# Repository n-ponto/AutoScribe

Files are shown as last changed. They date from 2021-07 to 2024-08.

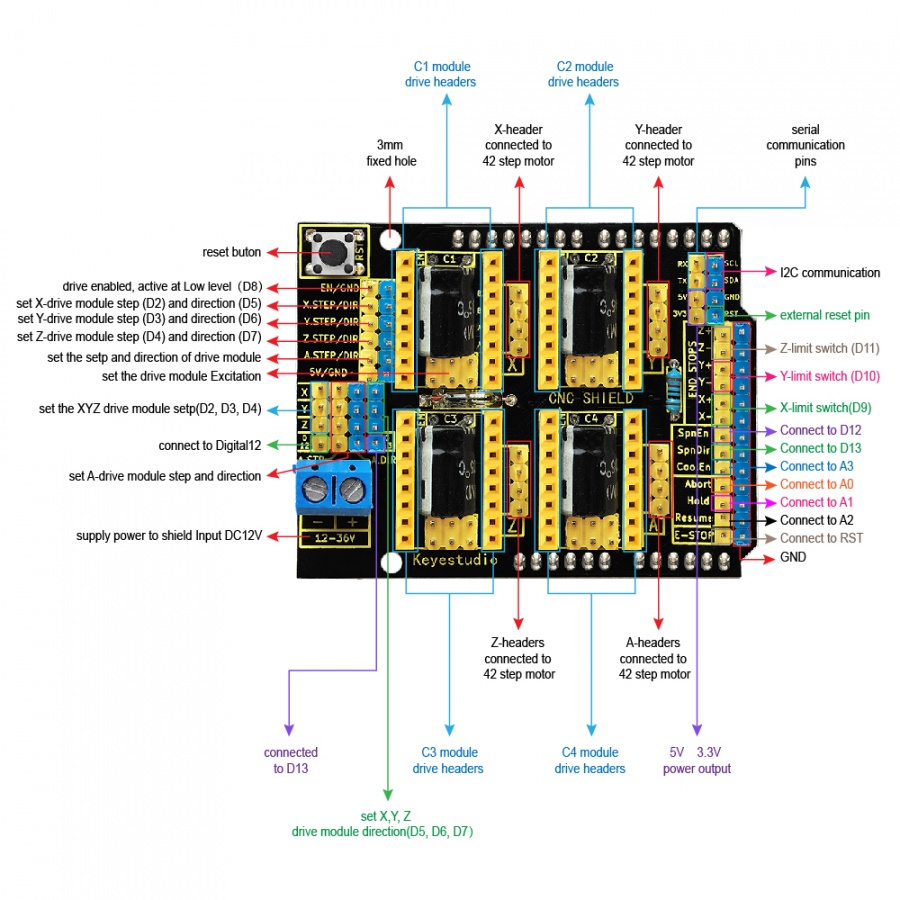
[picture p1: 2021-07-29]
images/cncsheild_wiring.jpg

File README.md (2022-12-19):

# AutoScribe

AutoScribe is a drawing machine capable of making any piece of art that can be drawn with pen on paper. On a PC, it converts scalable vector graphic (SVG) images into a set of points which are sent to the Arduino and drawn. 

## Video

Watch the video (https://youtu.be/xKn2pY1tWtM)

https://www.youtube.com/watch?v=xKn2pY1tWtM

# Background

## Inspiration

I was actually first inspired to work on this project because I enjoyed the feeling of handwritten notes, but was tired of hand cramps and sore wrists. If only there was a way to be able to combine the convenience of typing or dictating with the great feeling of pen on paper! Having seen 3D printers, laser cutters, and other CNC machines, I had the idea for a CNC drawing machine. After a quick search I found they already existed (no big suprise), but they were a bit pricy. I had some experience working with software, an Arduino, circuits, and 3D printing, how difficult would it really be to build one of these drawing machines myself? Turns out, it's actually pretty difficult -- especially when you're deadset on writing all the software yourself from scratch -- but that's why I think it's worth documenting my experience building this thing! 

## Refrences 

Along the way I found some sources which really helped get me off the ground and inspire some of my design choices:

**AxiDraw**

[AxiDraw](https://axidraw.com/) is a company which sells a range of similar writing and drawing machines. They seem to work extremely well and were a great proof of concept for me to justify the time I put into this project.

**Instructables 4xiDraw**

For most of the physical design of the machine I refrenced this instructables page titled [4xiDraw]((https://www.instructables.com/4xiDraw/)). At a glance the design is nearly the same, and I actually used the 3D models from that page in my first iteration of the hardware.

**Crazy Engineer’s Drawing Robot**

[CNC Drawbot](https://www.arnabkumardas.com/cnc.html) is another great refrence for a similar project. The page has a great bill of materials, and does things a bit different from 4xiDraw.

**Improvements in this Project** 

In my opinion, the physical design of the 3D printed parts for this project are quite a bit sleeker than others. I wanted to try to create a design took up minimal desk space and showed off the other pieces of hardware.

# Software

There are two main pieces of software for this project: (1) the C/C++ code that runs on the Arduino, and (2) the Python code that runs on a computer to convert SVGs into Ncode, send the Ncode to the Arduino, and actsas a GUI for easily using all the features of the drawing machine. 

## Arduino Code

This is all in the in the `Arduino_v2` directory, and check out the README in that directory to read more about the details of how the code works.

## Python Code

This code is mostly in the `Frames` and `Tools` directories. `Tools` contains most of the behind-the-scenes logic for converting SVGs into Ncode, sending Ncode to the Arduino, and some extra files for debugging and validating the results. `Frames` contains the code for the GUI. The `OverSerialTests` directory also has some lightweight code for testing the connection between the serial connection between the computer and the Ardiuno without needing to start the entire GUI.

# Graphical User Interface (GUI)

The GUI was written using the [tkinter](https://docs.python.org/3/library/tkinter.html) package. To start the GUI run 

```python ./GUI.py```

The GUI has 3 different tabs: Settings, Manual Control, and Drawing.

## Settings Tab

<img src="./readme_images/settings_tab.jpg" alt="Settings Tab Screenshot" width="300"/>

The settings tab is really just for adjusting the height of the pen, the "Up height" is the angle
of the pen's servo motor when the pen is off the paper, and "Down height" is when the pen is on the paper. As the angle increases the pen gets closer to the table. 

The user can use the arrow keys to fine tune these angles, and the pen on the machine will move in real time to make this process easier. When both the angles are correct pressing "Save angles" will preserve the current angles when drawing.

## Manual Control Tab

<img src="./readme_images/manual_control_tab.jpg" alt="Manual Control Tab Screenshot" width="300"/>

The manual control tab is mostly for debugging and playing around. It also uses the same pen height settings from the Settings Tab, so it's useful for checking that the pen height is correct for good ink flow while drawing. 

When not manually controlling or drawing, the stepper motors of the machine are unlocked and can be moved by hand. Once "Start manual control" is clicked, the motors will lock, and then the arrow keys can be used to control the motors. Pressing a single key will only move a single motor, (for example: pressing up and right will move both motors, up and down will do nothing). Because of the layout of the machine, when only one motor is moving, the pen will move diagonally with respect to the base. 

Holding the space bar will move the pen down to the paper.

## Drawing Tab

<img src="./readme_images/drawing_tab.jpg" alt="Manual Control Tab Screenshot" width="300"/>

The drawing tab is for selecting a `.ncode` file, vizualizing it, then sending to the Arduino. Clicking "Select File" will open a standard file selection dialog. Once a file is chosen, the path will appear where the "Please select a file" text is, and the "Vizualize" and "Send Ncode" buttons will unlock. 

Clicking the "Vizualize" button will create a new window to see what the Ncode should look like once drawn, like this: 

<img src="./readme_images/parrot_viz.jpg" alt="Manual Control Tab Screenshot" width="200"/>

Usually the vizualized images will appear more pixelated than you'd expect to see from the drawing machine. The light gray lines show the path the pen will take raised off the paper, and the blue lines show the path on the paper.

Clicking "Send Ncode" will immediately begin streaming commands to the drawing machine, and while drawing pressing "Cancel" will cause the machine to immediately stop.

# Hardware

The models for all the 3D printed pieces are in the `Models` directory. 

## Bill of Materials

| Count       | Name        | Notes        |
| --- | --- | --- |
| 1 | Arduino UNO | |
| 1 | USB cable | this should come with the Arduino
| 1 | CNC shield | connects the Arduino to the stepper motors
| 2 | Pololu stepsticks | these go on top of the CNC shield to interface with the stepper motors
| 2 | nema 17 stepper motors | 3D printer motors for moving the arm |
| 1 | micro servo SG90 | servo for moving the pen up and down |
| 1 | 12V 2A power supply | The USB connection from the computer won't be enough power for the stepper motors. Also, make sure this comes with the right connector to plug into the CNC shield somehow |
| 4 | 8mm smooth steel rods | whatever length you want for the drawing machine, I used 330mm |
| 8 | LM8UU | linear bearings for sliding along the smooth steel rods
| 2 | 20-tooth GT2 pulleys | go on top of the stepper motors for moving the belts
| 1 | GT2 belt | length depends on dimensions of your machine, can always cut one that's too long
| 10 | F623ZZ bearings | ball bearings for where the belt freely spins through the hub and by the pen |
| 2 | M10 threaded rods | these go through the two ends of the base to hold it together (have to be as long as the smooth steel rods)
| 8 | M10 nuts | two for each end of each rod |
| 8 | M10 washers | one for each M10 nut |
| X | Pack of M3 30mm, 16mm, 6mm screws, nuts, and washers | Need at least 8 of each screw, 12 nuts, and 4 washers
| 2 | 4mm OD x 100mm length rod | I used steel, 4xiDraw recommends carbon fiber. Pen slides along these. |
# Getting Started

All the info for downloading the software and getting started yourself.

## Installation

Specifications: Developed on Windows 10 using Python version 3.9.1

First clone the repo:

`git clone https://github.com/n-ponto/AutoScribe.git`

Then install the Python modules:

`pip install -r requirements.txt`

<details>
<summary>I recommend not trying to use Anaconda. Why not Anaconda?</summary>
<br>
Anaconda is a great tool to aid in Python package management.

<br>
I recommend not using Anaconda because there are some issues with installing the bezier module within the Anaconda environment. This is only required for the ParseSvg.py script, so if you don't plan to create any of your own images and just rely on the ncode files already provided in this repo, then there's no need to install the bezier module.
</details> <br> 

## Uploading to the Arduino
In order to upload the C++ code to the Aruino, the easiest way is to use the [Arduino IDE](https://www.arduino.cc/en/software). From the Aruino IDE, you'll want to open the main file at `Arduino_v2/Arduino_v2.ino`. This should open the entire Arduino project (all the files in the `Arduino_v2` folder). Then upload the code by clicking the right arrow in the top left corner of the IDE.

# Creating New Images

### Creating SVG files

Creating an SVG file is the first step in drawing something. All that really matters in this file is the Path objects, because these are what get turned into Ncode. I like using the free software [Inkscape](https://inkscape.org/) for making and working with SVGs. Inkscape has a built-in "Trace Bitmap" function to get a SVG path from a standard raster image. Usually I find that I need to manually touch up the SVG paths a bit after using this tool.

### Converting SVG files to NCODE

Once you have an SVG of a file you'd like to draw, it needs to be converted to Ncode. To do this, run:

```
python ParseSvg.py path/to/file.svg
```

`ParseSvg.py` can also directly vizualize the ncode or can take a custom save path for the Ncode file. For more info, use:
```
py ParseSvg.py -h
```

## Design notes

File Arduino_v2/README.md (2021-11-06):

# Arduino

## Overview
This is the code to run on the Arduino. It's responsible for accepting commands
from the computer over serial communication and controlling the two stepper and
one servo motors which make up the drawing machine. By accepting commands from
the computer it's able to draw images using a pen.

---

# Technical Details

## Runtime Modes
These influence how the Arduino reads information from the serial and
acts on that information.

**1. [Accepting Commands](#accepting-commands-mode)** - listens for commands over serial.

**2. [Manual Control](#manual-control-mode)** - used to manually control the movement of drawing machine in real time

**3. [Drawing](#drawing-mode)** - used to draw an image by interpreting instructions over serial

## Accepting Commands mode
Listens to serial connection for one byte commands from the list of commands below. Generally, if the command can be completed quickly or requires reading a predetermined amount of data from serial, it is executed in the Accepting Commands runtime mode before listening for the next command. If the command is to switch commands, then the Arduino will switch remain in the other runtime mode until receiving a signal to return to this mode.

| Command | Description |
| --- | --- |
| SET_PEN_RANGE | Used to define the top and bottom boundaries of the pen's movement. Will listen for two more bytes, one byte each for the minimum and maximum angle for the pens movement.  |
| CHANGE_PEN_ANGLE | Used to immediately change the current angle of the pen. This can be useful when trying to determine the optimal pen range. It will listen for one more byte for the angle to move the pen (i.e. the servo motor). | 
| MOVE_TO_COORDINATE | Used to immediately change the current location of the pen. It will listent for 4 total more bytes, two 2B integers for the x and y coordinates. | 
| RESET_HOME | Used to reset the home value of the steppers. When this command is executed the current location of the end effector will be considered the origin. |
| ENTER_DRAW_MODE | Will go into Drawing mode.  |
| ENTER_MANUAL_CONTROL_MODE | Will go into Manual Control mode. |
| SET_STEPPER_DELAY | Sets the delay between signals to the steppers. This value is directly related to the movement speed of the steppers. Should be calibrated to optimize between speed and minimal shaking. |

## Manual Control mode
After entering this mode, it will continuously listen for single byte packets indicating how to move. These instructions will either move the pen up/down, or will indicate how to move the steppers. If this mode receives the instruction to stop, it will return to the accepting commands mode.

## Drawing mode 
After entering this mode, it will continuously listen for 4 byte packets, where each packet will contain a set of two 2-byte coordinates.

The maximum coordinate range of the drawing machine can be represented using only 11-bits, meaning that each 16-bit coordinate dimension has 5 bits left over. These extra bits are used to encode additional information: pen up, pen down, and to end drawing mode.

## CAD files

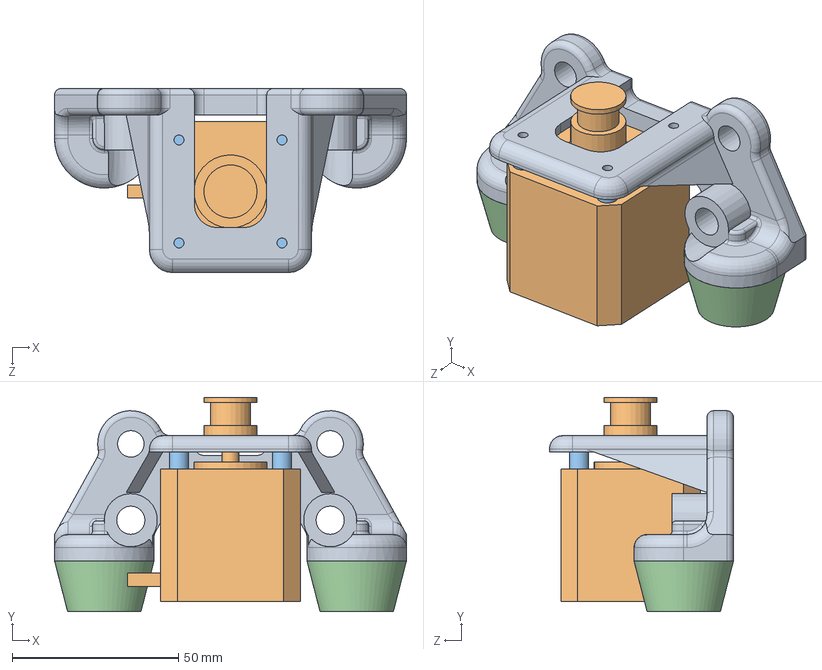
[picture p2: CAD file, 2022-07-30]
models/assembly_legs.SLDASM
105.9 x 64.5 x 55.4 mm
legs
stepper
anti-vibration screw x 4
rubber foot^assembly_legs x 2

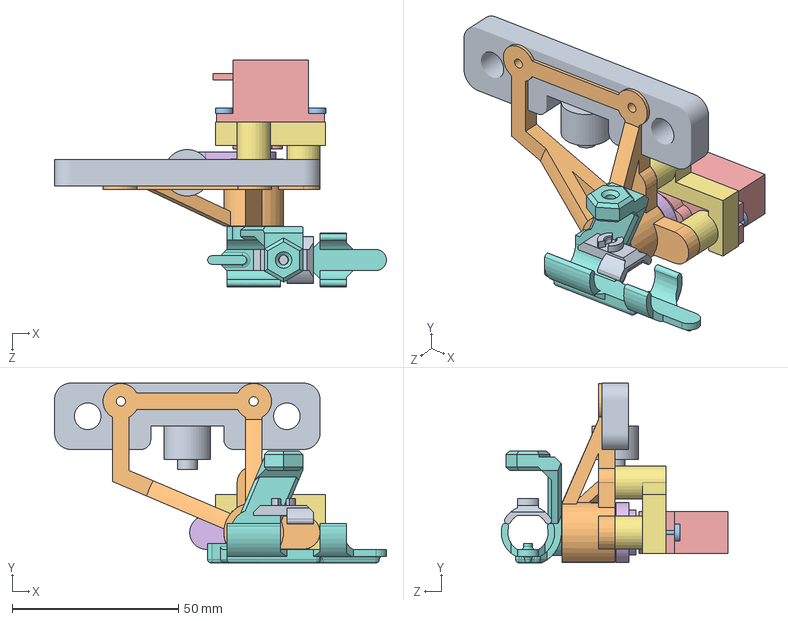
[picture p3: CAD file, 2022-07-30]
models/end_effector/v2/end_effector_assembly_v2.SLDASM
100.0 x 54.2 x 68.2 mm
mount^end_effector_assembly_v2
servo_screw x 2
servo_arm
servo
driver^end_effector_assembly_v2
servo_mount^end_effector_assembly_v2
pen holder^end_effector_assembly_v2
pen_press^end_effector_assembly_v2

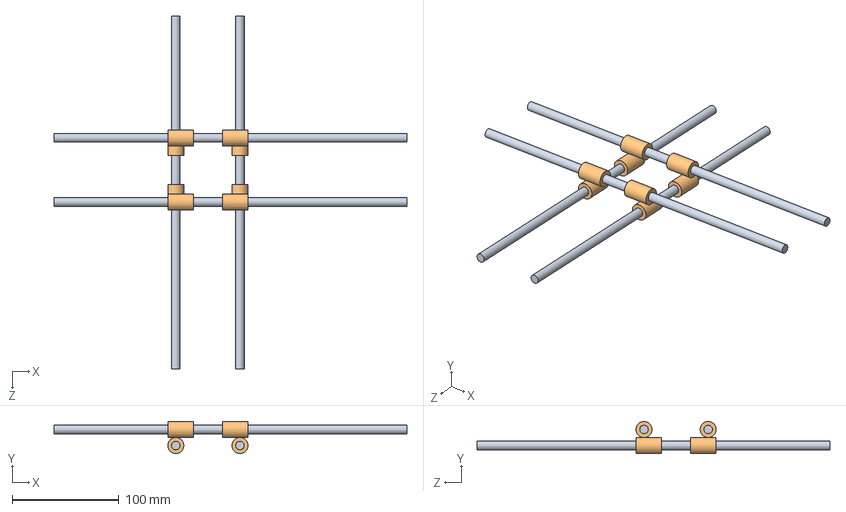
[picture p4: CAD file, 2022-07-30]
models/hub/slider_refrence/slider.SLDASM
330.0 x 30.0 x 330.0 mm
rod x 4
linear_bearing x 8

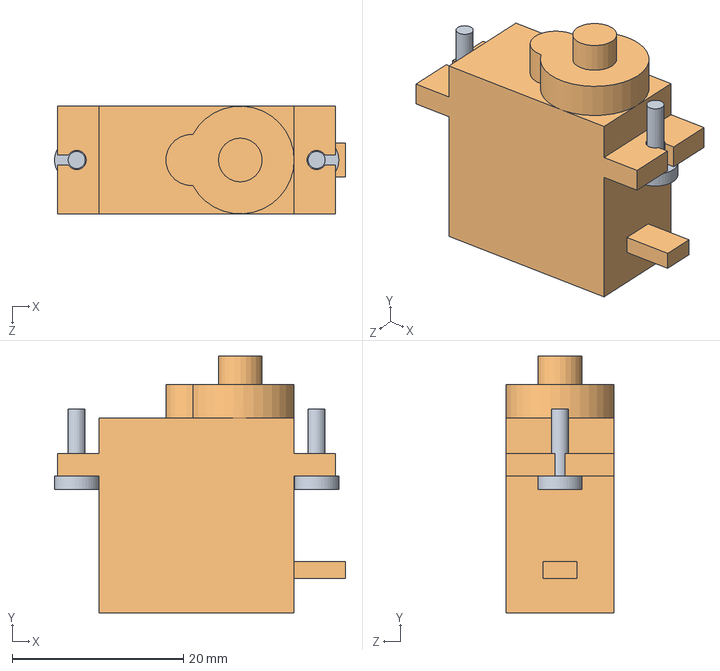
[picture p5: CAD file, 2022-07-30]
models/servo/servo_assembly.SLDASM
34.0 x 30.0 x 12.6 mm
servo_screw x 2
servo

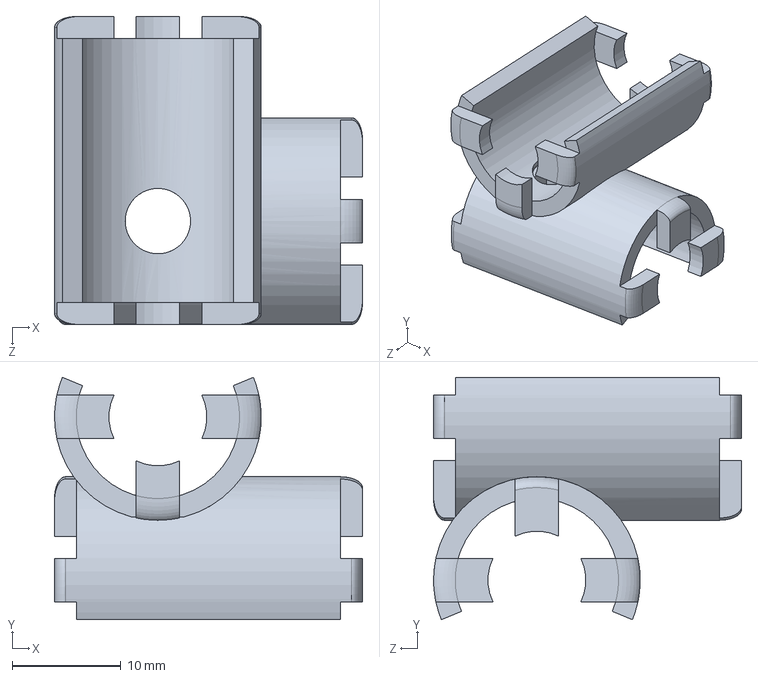
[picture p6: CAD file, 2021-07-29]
models/hub/bottom/stackedbearingleft_v1.SLDASM
28.3 x 22.3 x 28.3 mm
singlebearing_v1 x 2

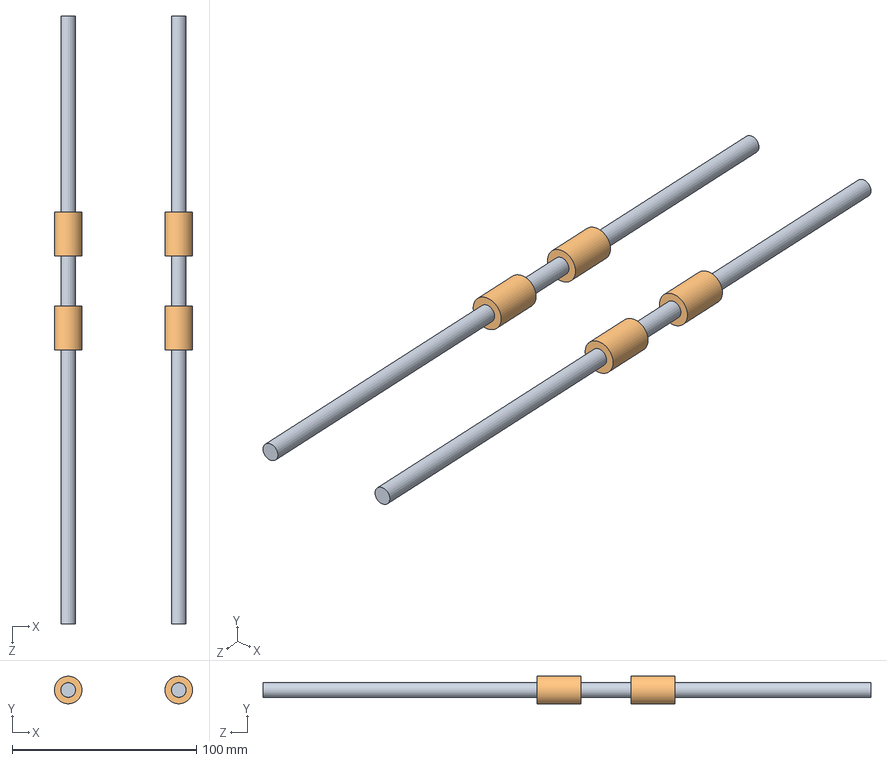
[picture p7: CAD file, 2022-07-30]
models/hub/slider_refrence/single_axis.SLDASM
75.0 x 15.0 x 330.0 mm
rod x 2
linear_bearing x 4

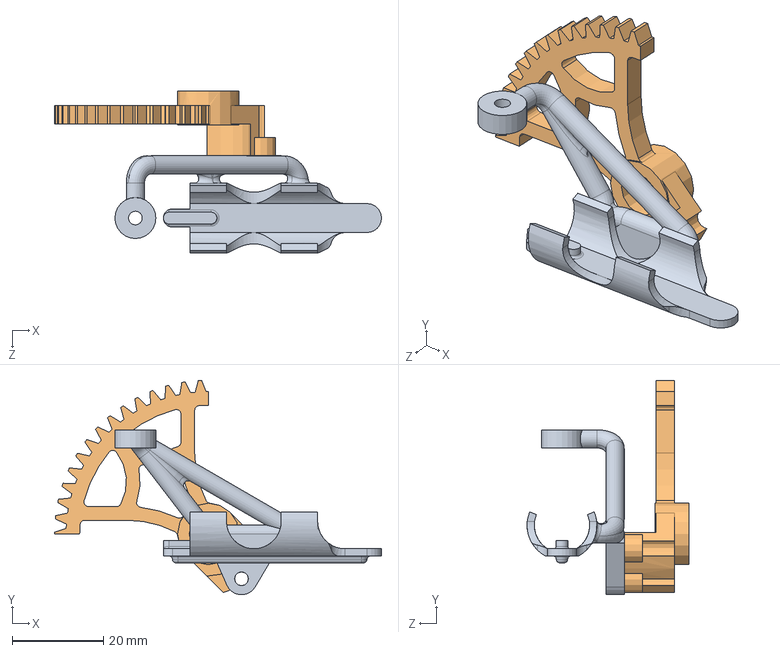
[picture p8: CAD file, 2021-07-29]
models/end_effector/depreciated/geared_ee/pen_gear_assembly.SLDASM
71.8 x 47.1 x 35.5 mm
pen_holder
long_gear

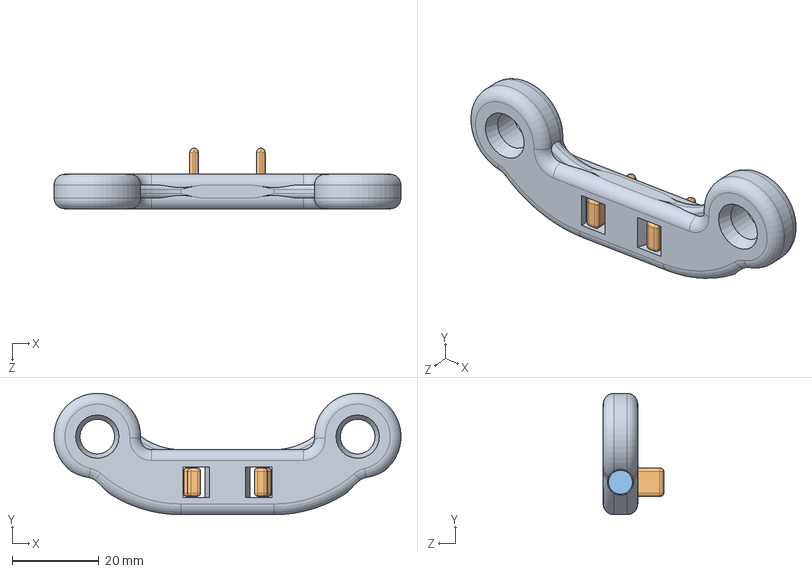
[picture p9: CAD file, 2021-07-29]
models/endy/endy_assembly.SLDASM
80.0 x 28.0 x 14.0 mm
endy_v2
pincher x 2
10MM M3 screw x 2

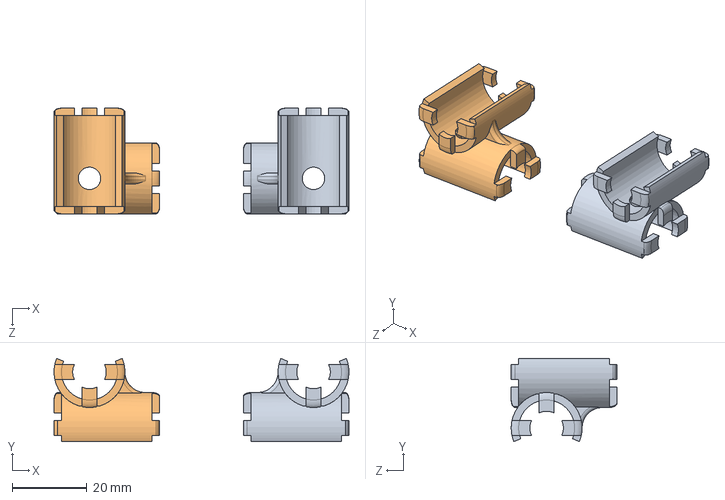
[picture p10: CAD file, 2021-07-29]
models/hub/bottom/frontbearing_v1.SLDASM
79.0 x 22.3 x 28.3 mm
stackedbearingright
stackedbearingleft_v1

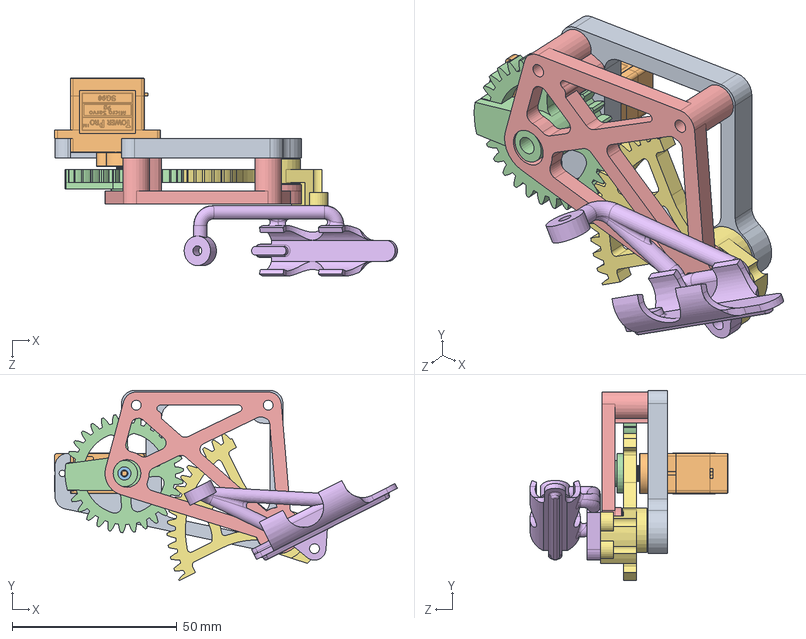
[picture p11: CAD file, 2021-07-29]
models/end_effector/depreciated/geared_ee/full_assembly.SLDASM
104.0 x 57.7 x 60.1 mm
base_mount
SG90 - Micro Servo 9g - Tower Pro.1
SG90 - Micro Servo 9g - Tower Pro.2
power_gear
exterior^full_assembly
pen_holder
long_gear

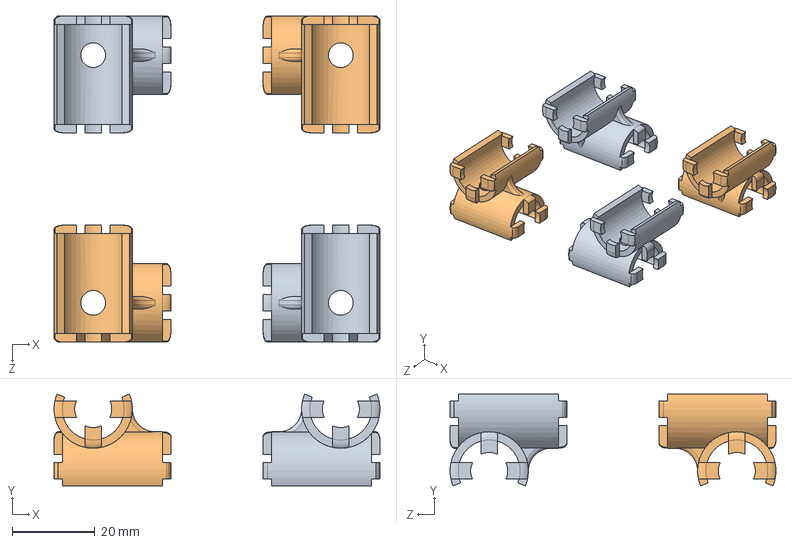
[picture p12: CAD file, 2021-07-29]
models/hub/bottom/allbearing.SLDASM
79.0 x 22.3 x 79.0 mm
stackedbearingright x 2
stackedbearingleft_v1 x 2

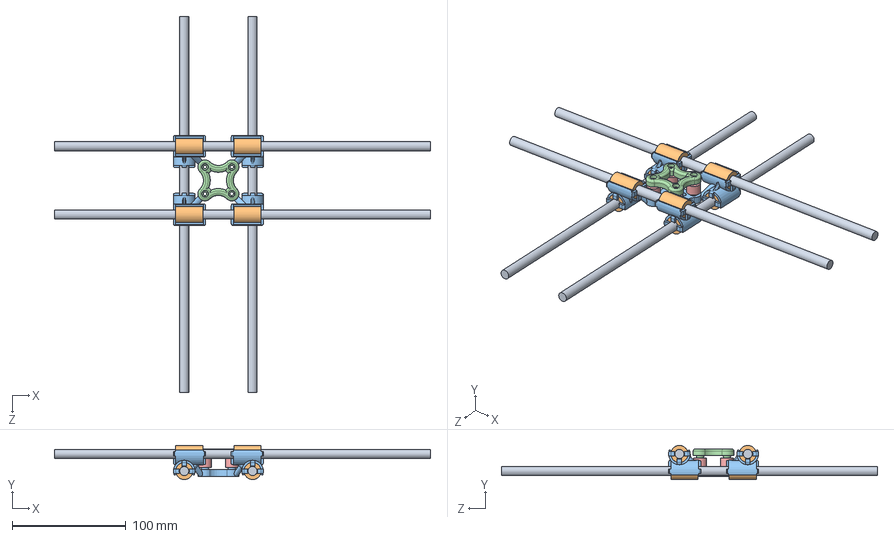
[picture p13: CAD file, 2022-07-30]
models/hub_assembly.SLDASM
330.0 x 30.0 x 330.0 mm
rod x 4
linear_bearing x 8
mountingbase
top
internal_bearing x 4

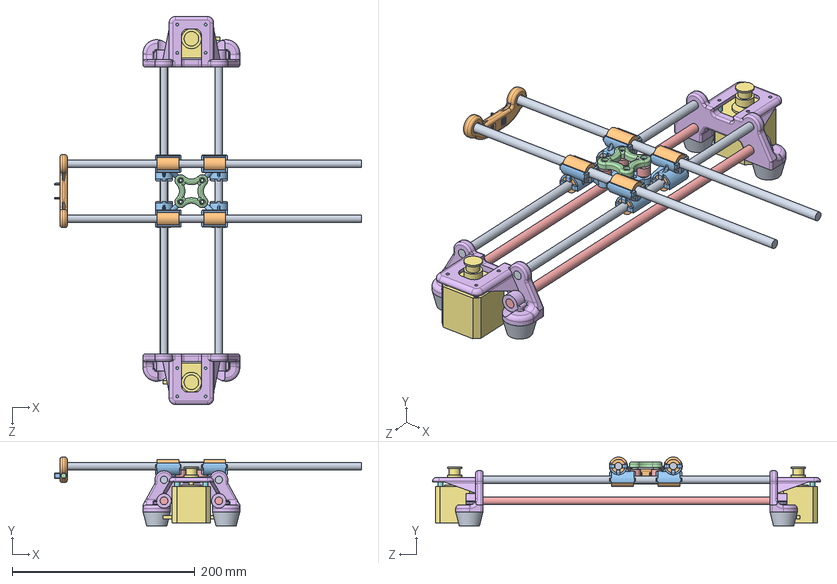
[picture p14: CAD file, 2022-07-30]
models/assembly_whole.SLDASM
336.0 x 75.5 x 424.8 mm
rod x 4
linear_bearing x 8
mountingbase
top
internal_bearing x 4
legs x 2
stepper x 2
anti-vibration screw x 8
rubber foot^assembly_legs x 4
endy_v2
pincher x 2
10MM M3 screw x 2
threaded rod^assembly_whole x 2

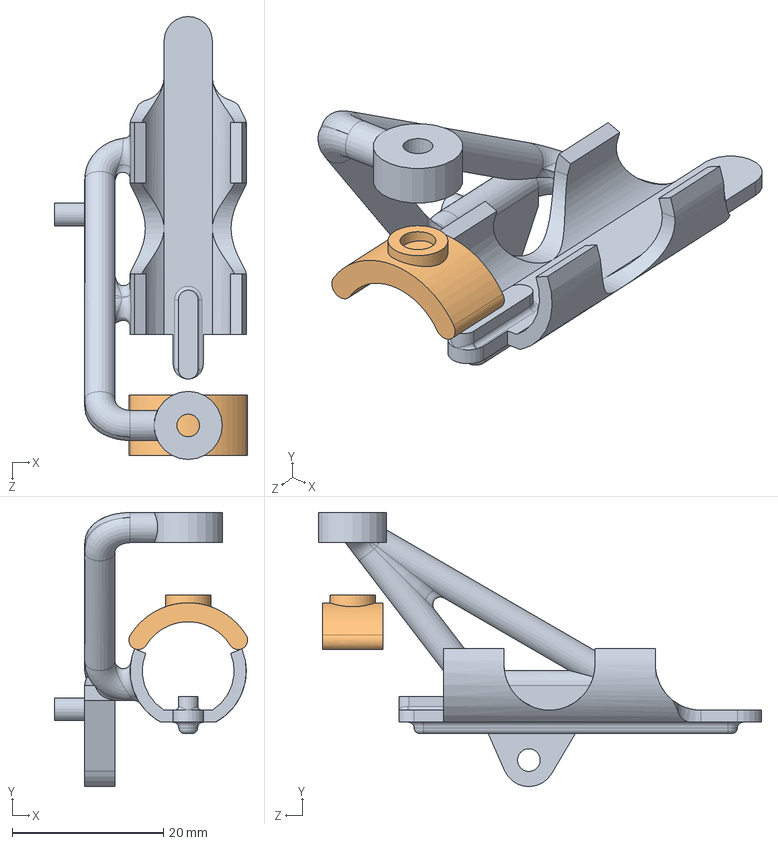
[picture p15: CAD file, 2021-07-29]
models/end_effector/depreciated/geared_ee/pen_assembly.SLDASM
25.5 x 36.2 x 58.5 mm
pen_holder
pen_cup^pen_assembly

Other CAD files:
models/endy_assembly.SLDASM
models/hub/bottom/stackedbearingright_v1.SLDASM
models/hub/bottom/hub_assembly.SLDASM
models/ee_assembly.SLDASM
models/anti-vibration screw.SLDPRT
models/assembly_end_effector.SLDASM
models/drivetrain.SLDPRT
models/ee_axis_mount.SLDPRT
models/end_effector/depreciated/geared_ee/SG90 - Micro Servo 9g - Tower Pro.1.SLDPRT
models/end_effector/depreciated/geared_ee/SG90 - Micro Servo 9g - Tower Pro.2.SLDPRT
models/end_effector/depreciated/geared_ee/base_mount.SLDPRT
models/end_effector/depreciated/geared_ee/long_gear.SLDPRT
models/end_effector/depreciated/geared_ee/pen_gear.SLDPRT
models/end_effector/depreciated/geared_ee/pen_holder.SLDPRT
models/end_effector/depreciated/geared_ee/power_gear.SLDPRT
models/end_effector/depreciated/geared_ee/servo.SLDPRT
models/end_effector/depreciated/mounted_holder.SLDPRT
models/end_effector/depreciated/servo_interface.SLDPRT
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

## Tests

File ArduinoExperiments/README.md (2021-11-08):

# Arduino Experiments

These files are intended to be used to test some of the functionality of the arduino is a smaller environment. 

Timers.ino
: some experiments and proof of concepts for using the TimerOne library to implement interrupt functions. 

PointerSize.ino
: some sanity checks to determine the size in bytes of different primatives on the Arduino board

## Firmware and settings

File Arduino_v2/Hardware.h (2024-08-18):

/*
Constants for hardware pins, constant values, and defaults
*/
#ifndef HARDWARE_H_
#define HARDWARE_H_

#include <Arduino.h>

// Stepper pins
#define TOP_STP_PIN 3     // Pin for stepping the top motor
#define TOP_DIR_PIN 6     // Pin for changing the top motor direction
#define BOT_STP_PIN 2     // Pin for stepping the bottom motor
#define BOT_DIR_PIN 5     // Pin for changing the bottom motor direction
#define ENABLE_PIN 8      // Pin to enable both motors
#define HALF_STEP_PIN A0  // Pin to enable half stepping
#define QRTR_STEP_PIN 4   // Pin to enable quarter stepping
#define SCREEN_RST 52
#define SCREEN_CE 53
#define SCREEN_DC 51
#define SCREEN_DIN 49
#define SCREEN_CLK 47

// Pen servo pin
#define SERVO_PIN 10  // Pin for the servo motor holding the pen

// Spin directions
#define CW LOW    // Direction value to turn clockwise
#define CCW HIGH  // Direction value to turn counter-clockwise
// Stepper enable values
#define ENABLE_STEPPERS LOW
#define DISABLE_STEPPERS HIGH

// LCD screen settings
#define SCREEN_UPDATE_PERIOD 300  // Time in milliseconds between screen updates
#define SCREEN_CONTRAST 0xBF
#define SCREEN_BIAS 0x13
#define SCRN_CH_WD 7  // Width of a character in pixels
#define SCRN_WD 84    // Width of the screen in pixels

// Defaults
#define DEFAULT_UP 50               // Angle for when the pen is up off the paper
#define DEFAULT_DOWN 70             // Angle when pen is down on the paper
#define DEFAULT_STEPPER_DELAY 2000  // Microsecond delay between stepper pulses
#define DEFAULT_DRAWING_SPEED 250   // Default speed for the stepper motor while drawing
#define DEFAULT_PEN_DELAY 300       // Millisecond delay to pause while the pen goes up/down
#define SPEED_MULTIPLIER 1          // Multiplier to convert from mm/s to whole-steps/s
#define MIN_STEPS_PER_SEC 500       // Minimum steps per second for the stepper motor
#define MAX_MICROSTEP 8             // Maximum microstepping setting

// Serial communication signals
#define DRAW_DONE 0xAB
#define DRAW_START_SENDING 0xFA
#define DRAW_BUFFER_EMPTY 0xFF
#define HANDSHAKE 0x55

void penDraw();
void penMove();
void updateStepperSpeed(uint16_t speed);

#endif  // HARDWARE_H_

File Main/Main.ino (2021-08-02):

// CNC Shield Stepper  Control Demo
// Superb Tech
// www.youtube.com/superbtech

// X axis   step: 2     direction: 5
// Y axis   step: 3     direction: 6

#include <Servo.h>
#include "StepperController.h"
#include "Transceiver.h"



long lastUpdate = 0;
const long toggleDelay = 2000;

// Servo
const int ServoPin = 11;  // PWM pin for the servo
int servoAngle = 70;
Servo servo;
bool penDown = false;

// Joystick
const int X_pin = 0;
const int Y_pin = 1;
const int SW_pin = 13;

StepperController sc;
Transceiver tcvr;

const int cutoff = 180; // difference in joystick reading to ignore
const int loRange = (512-cutoff), hiRange = (512+cutoff);
void handleJoystick()
{
    bool sw = digitalRead(SW_pin);
    int x = analogRead(X_pin);
    int y = analogRead(Y_pin);

    if (sw && toggleDelay < millis() - lastUpdate ) 
    {
        Serial.println("move pen");
        servoAngle = penDown ? 110 : 130;
        servo.write(servoAngle);
        penDown = !penDown;
        lastUpdate = millis();
    }

    // Readings range from 0-1023 (center 512)
    // Y=0 -> UP  X=0 -> RIGHT
    bool u, d, l, r;
    d = y < loRange;
    u = y > hiRange;
    r = x > hiRange;
    l = x < loRange;

    // Disable if not receving commands
    if (!(u || d || l || r)) 
    {
        sc.disable();
        return;
    }

    sc.enable();
    Direction dir = (u << 3) + (d << 2) + (l << 1) + r;
    Serial.print("direction: ");
    Serial.print(dir);
    // sc.move(dir, 1);
}

void readSerialForPoint()
{
    if (Serial.available() >= sizeof(Point))
    {
        Point pt;
        Serial.readBytes((char *)(&pt), sizeof(Point) );
        Serial.println("(" + String(pt.x) + ", " + String(pt.y) + ")");
        Serial.println("Bytes left: " + String(Serial.available()));
        Serial.readString();
        sc.enable();
        sc.travel(pt);
        sc.disable();
    }
}

char c[2];
void setup() {
    sc.initialize();
    tcvr.initialize(&sc, &servo);
    // Servo
    servo.attach(ServoPin);
    servo.write(servoAngle);
    // Joystick
    // pinMode(SW_pin, INPUT);
    // X and Y pins are analog & auto input
}

// TESTING FUNCTIONS
void readStepsAndSqureDiamond();
void readAndTravelToCoordinates();
void testTheory();
void testSerialCom();

int steps;

void loop() 
{
    tcvr.handle();
}

/*******************************************************************************
*******************************************************************************/

void readStepsAndSqureDiamond()
{
    if (Serial.available())
    {
        steps = Serial.parseInt();
        Serial.readBytes(c, 2);
        if (steps < 1)
        {
            sc.resetHome();
        }
        else 
        {
            Serial.print("Moving ");
            Serial.print(steps);
            Serial.println(" steps.");
            sc.enable();
            sc.square(steps);
            sc.diamond(steps);
            sc.disable();
        }
    }
}

char inarr[10];
void readAndTravelToCoordinates()
{
    if (Serial.available())
    {   
        Point pt; 
       
        pt.x = Serial.parseInt();
        pt.y = Serial.parseInt();
        Serial.readBytes(c, 2);
        Serial.println("Received: (" + String(pt.x) + ", " +  String(pt.y) + ")");
        sc.enable();
        sc.travel(pt);
        sc.disable();
    }
}


void testTheory()
{
    if (Serial.available())
    {
        while(Serial.available()) { Serial.read(); }
        Serial.readBytes(c, 2);
        Point p1, p2, p3;
        p1.x = 400; p1.y = 400;
        p2.x = 400; p2.y = 200;
        p3.x = 200; p3.y = 200;  
        sc.enable();
        sc.travel(p1);
        sc.travel(p2);
        sc.travel(p3);
        sc.disable();
        sc.position.x = sc.position.y = 0;
    }
}

char incoming[10];
// char *world = "world!";
void testSerialCom()
{
    if (Serial.available() >= sizeof(Point))
    {
        Serial.println("Bytes to read: " + String(Serial.available()));
        Point pt;
        Serial.readBytes((char *)(&pt), sizeof(Point) );
        Serial.println("(" + String(pt.x) + ", " + String(pt.y) + ")");
        Serial.println("Bytes left: " + String(Serial.available()));
        Serial.readString();
    }
}

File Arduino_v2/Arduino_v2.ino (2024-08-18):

/*
Main file for the Arduino code
Contains:
- startup and loop functions
- shared buffer for the drawing and manual control modes
- list of functions for the runtime modes
*/
#include <Arduino.h>
#include <NOKIA5110_TEXT.h>
#include <Servo.h>
#include <TimerTwo.h>

#include "Commands.h"
#include "Hardware.h"
#include "RuntimeModes.h"

void (*runtime_mode)(void);  // Function to call the current runtime mode

Servo penServo;
NOKIA5110_TEXT lcdScreen(SCREEN_RST, SCREEN_CE, SCREEN_DC, SCREEN_DIN, SCREEN_CLK);

uint8_t penUpAngle, penDownAngle;  // Angle for the pen servo to be up and down
uint16_t stepperPeriodDrawing;     // Microsecond delay between stepper pulses when drawing
uint16_t stepperPeriodMoving;      // Microsecond delay between stepper pulses when moving
uint8_t mstepMulti;                // Multiplier for microstepping (1, 2, 4, 8, or 16)
bool penUp;                        // True if the pen is up, false if the pen is down

void (*changeDrawStepFn)();  // Function to change the microstepping mode for drawing

/// @brief Initialize pins and set default values for hardware to avoid undefined behavior
void hardwareInit() {
  Serial.begin(9600);
  // Initilize the stepper pins
  pinMode(TOP_STP_PIN, OUTPUT);
  pinMode(TOP_DIR_PIN, OUTPUT);
  pinMode(BOT_STP_PIN, OUTPUT);
  pinMode(BOT_DIR_PIN, OUTPUT);
  pinMode(ENABLE_PIN, OUTPUT);
  pinMode(HALF_STEP_PIN, OUTPUT);
  pinMode(QRTR_STEP_PIN, OUTPUT);
  digitalWrite(ENABLE_PIN, DISABLE_STEPPERS);
  // initialize the pen servo pin
  penUpAngle = DEFAULT_UP;
  penDownAngle = DEFAULT_DOWN;
  penServo.attach(SERVO_PIN);
  penServo.write(20);
  // initialize stepper motors
  stepperPeriodMoving = DEFAULT_STEPPER_DELAY;
  updateStepperSpeed(DEFAULT_DRAWING_SPEED);
  // timer for interrupts and runtimeMode
  Timer2.init(stepperPeriodDrawing, NULL);
  runtime_mode = acceptingCommands;
}

void setup() {
  hardwareInit();

  waitForConnection();
}

void loop() {
  // Call the function for the current runtime mode
  runtime_mode();
}

void setRuntimeMode(void (*fn)(void)) {
  runtime_mode = fn;
}

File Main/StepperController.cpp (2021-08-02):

#include <Arduino.h>
#include "StepperController.h"

void StepperController::initialize()
{
    Serial.println("Stepper controller initialized.");
    pinMode(STEP_TOP, OUTPUT);
    pinMode(DIR_TOP,  OUTPUT);
    pinMode(STEP_BOT, OUTPUT);
    pinMode(DIR_BOT,  OUTPUT);
    pinMode(ENABLE,OUTPUT);
    digitalWrite(ENABLE, HIGH); // disable at the beginning
    wait = 700;
    enabled = false;
    resetHome();
}

void StepperController::move(Direction d, uint16_t steps)
{
    if (d < 1 || d > 12)
    {
        // Can't be zero or have 3 bits selected
        return;
    }
    
    // If only one then both steppers will have to work
    bool b, t;
    switch(d)
    {
        case (UP):    t = b = CW;      break;
        case (DOWN):  t = b = CCW;     break;
        case (LEFT):  t = CCW; b = CW; break;
        case (RIGHT): t = CW; b = CCW; break;
        default:
            // Two directions selected
            bool spin = d & DOWN;
            bool stepper = (d & RIGHT) ^ spin;
            uint8_t stepPin = stepper ? STEP_TOP : STEP_BOT;
            uint8_t dirPin =  stepper ? DIR_TOP  : DIR_BOT;
            digitalWrite(dirPin, spin);
            // If we're moving only one stepper we have to move it twice as far
            for (uint16_t i = 0; i < steps*2; i++)
            {
                // Set one high
                digitalWrite(stepPin, HIGH);
                delayMicroseconds(wait);
                // Set one low
                digitalWrite(stepPin, LOW); 
                delayMicroseconds(wait);
            }
            return;
    }
    // Only one of the directions was selected

    // Set direction for both
    digitalWrite(DIR_TOP, t);
    digitalWrite(DIR_BOT, b);
    // Step both
    for (uint16_t i = 0; i < steps; i++)
    {
        // Set both high
        digitalWrite(STEP_TOP, HIGH);
        digitalWrite(STEP_BOT, HIGH);
        delayMicroseconds(wait);
        // Set both low
        digitalWrite(STEP_TOP, LOW);
        digitalWrite(STEP_BOT, LOW); 
        delayMicroseconds(wait);
    }
}

bool StepperController::areEnabled()
{
    return enabled;
}

void StepperController::enable()
{ 
    if (!enabled)
    {
        Serial.println("Steppers enabled");
        enabled = true;
        digitalWrite(ENABLE, LOW);
    } 
}

void StepperController::disable()
{
    if (enabled)
    {
        Serial.println("Steppers disabled");
        enabled = false;
        digitalWrite(ENABLE, HIGH);
    }
}

void StepperController::square(uint16_t steps)
{
    move(UP, steps);
    move(RIGHT, steps);
    move(DOWN, steps);
    move(LEFT, steps);
}

void StepperController::diamond(uint16_t steps)
{
    move(UP + RIGHT, steps);
    move(DOWN + RIGHT, steps);
    move(DOWN + LEFT, steps);
    move(UP + LEFT, steps);
}

void StepperController::resetHome()
{
    disable();
    Serial.println("Resetting home coordinates...");
    position.x = position.y = 0;
    printCoordinates();
}

void StepperController::printCoordinates()
{
    String output = "Current position: (" + String(position.x) + ", " + String(position.y) + ")\n";
    Serial.print(output);
}

void StepperController::travel(const Point &pt)
{
    int16_t x, y;
    x = pt.x - position.x;
    y = pt.y - position.y;
    localTravel(x, y);
    position.x = pt.x;
    position.y = pt.y;
    printCoordinates();
}

void StepperController::localTravel(int16_t x, int16_t y)
{
    Serial.println("Travelling locally to: (" + String(x) + ", " + String(y) + ")");
    bool back = x < 0;
    bool down = y < 0;
    int16_t absx, absy;
    absx = back ? -1*x : x;
    absy = down ? -1*y : y;
    bool steep = absy > absx;

    // Set the output command
    Direction x_chng, y_chng;
    x_chng = back ? LEFT : RIGHT;
    y_chng = down ? DOWN : UP;
    Direction moveOne, moveBoth;
    moveBoth = x_chng + y_chng;
    moveOne = steep ? y_chng : x_chng;

    // Check if need to switch x and y
    if (steep){
        int16_t save = absx;
        absx = absy;
        absy = save; 
    }

    int16_t m, slope_error, c;
    m = 2 * absy;
    slope_error = m - absx;
    c = slope_error - absx;
    for (int16_t i = 0; i < absx; i++)
    {
        if (slope_error >= 0)
        {
            move(moveBoth, 1);
            slope_error += c;
        }
        else
        {
            move(moveOne, 1);
            slope_error += m;
        }
    }



}

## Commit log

2021-07-29 started adding coordinates to stepper controller
2021-07-30 end effector redesign
    [SG90 - Micro Servo 9g - Tower Pro.1.SLDPRT, SG90 - Micro Servo 9g - Tower Pro.2.SLDPRT, base_mount.SLDPRT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]
2021-07-30 end effector reorganize
    [EndY.SLDPRT, SG90 - Micro Servo 9g - Tower Pro.1.SLDPRT, SG90 - Micro Servo 9g - Tower Pro.2.SLDPRT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]
2021-07-31 line drawing algorithm
    [end_effector_assembly_v2.SLDASM, pen_press.3mf, servo_assembly.SLDASM]
2021-07-31 updated line drawing algorithm and converted to arduino
2021-07-31 clean up files
    [pen_press.3mf]
2021-08-10 Started working on Drawing frame
2021-08-11 arduino code for drawing mode
2021-11-08 added serial testing file for arduino
2021-11-12 started implementing drawing stepper hardware logic
2021-11-14 Updated camel case
2021-12-11 generate and print ncode files
2021-12-23 finisehd adding pen delay to interrupt function
2022-01-03 manual control working with pen and timer2
2022-07-30 push summer 2022
    [SG90 - Micro Servo 9g - Tower Pro.1.SLDPRT, SG90 - Micro Servo 9g - Tower Pro.2.SLDPRT, anti-vibration screw.SLDPRT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]
2022-07-30 - created cmdlets - moved frames from seperate folder - added state restoration to GUI - vizualizer unrotates the ncode coordinates - svgparser uses svg.parse library
    [settings.obj]
2022-08-05 - simplification logic for traversing segments - decreased pen delay on hardware - added naive cancel button in drawing frame - added ncode files to repo - tuned NcodeSender parameters
    [settings.obj]
2022-08-11 removed screen working
    [settings.obj]
2022-08-11 - removed unused commands from arduino - inits saved pen angles to arduino
2022-08-11 - removed unused commands from arduino - init saved settings upload to arduino
2024-08-02 Thread for sending ncode
2024-08-18 handshake start, caches stepper speed
